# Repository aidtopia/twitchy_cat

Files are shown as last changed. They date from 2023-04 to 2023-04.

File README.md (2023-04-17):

# Twitchy Cat
Adrian McCarthy (mechanics)  
Suzanne Coberly (corpsing)  
based on Oak Lane Cemetery's [Undead Kitty][1]

## The Effect

A rotting corpse of a cat sporadically kicks its hind legs.  It's gruesome and may bother cat lovers.

## Documentation

* [Assembly][2]
* [Corpsing][3]

## Parts

The assembly and corpsing instructions contain lists of all the parts and supplies used for our version.

There are two additional parts that can be printed with a 3D printer.  They are optional, but highly recommended if you're trying to replicate our version.

* Twitchy Cat Link ([STL][4] [SCAD][5]) simplifies fabrication of a reliable linkage
* Handheld Button ([STL][6] [SCAD][7]) provides a tidy case for a push button controller

Oak Lane Cemetery used a prop controller circuit from Jekyll-Labs.  As of this writing, Jekyll-Labs offers a newer version of that circuit called the [Twitchboard][8].

[1]: https://youtu.be/KJrArt0GAYc
[2]: https://github.com/aidtopia/twitchy_cat/blob/main/documentation/twitchy_cat_assembly.md
[3]: https://github.com/aidtopia/twitchy_cat/blob/main/documentation/twitchy_cat_corpsing.docx
[4]: https://www.printables.com/model/455279-twitchy-cat-link
[5]: https://github.com/aidtopia/twitchy_cat/blob/main/parts/twitchy_cat_link.scad
[6]: https://www.printables.com/model/430824-handheld-button
[7]: https://github.com/aidtopia/twitchy_cat/blob/main/parts/handheld_button.scad
[8]: https://www.jekyll-labs.com/p/twitchboard-prop-controller-with.html

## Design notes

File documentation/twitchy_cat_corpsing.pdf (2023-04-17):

## Twitchy Kitty Corpsing & Making Movable Joints

I. First step – Adding movement with actuator and spring (see Adrian’s write up/video)- this could be done later in the process as well, either after making movable joints and dry brushing or after initial corpsing. Either works!

II. Second step – making movable joints and adjusting leg/head position.

a. The way the cat skeleton comes, you cannot move most of the
| joints at all and cannot easily achieve the look of a curled up dead cat as done by Oak Lane Cemetery. The cat has straight legs, and this looks quite different from the classic “undead kitty” (figure 1). If you are OK with this, feel free to skip this step as it does add time; just remember it will be difficult to change your mind after you have done all the corpsing and finishing.

Fig. 1- Top: Unaltered cat skeleton; Middle: “Undead Kitty” from Oak Lane Cemetery after finishing; Bottom: My version of cat skeleton dry brushed with movable joints (back spine has not yet been cut).

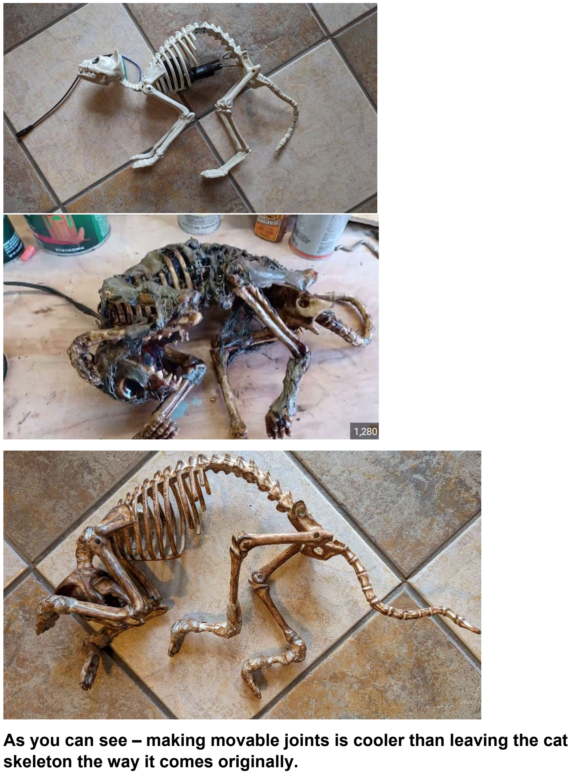
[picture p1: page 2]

As you can see – making movable joints is cooler than leaving the cat skeleton the way it comes originally.

b. Initial steps: Some of the joints (hips, shoulders, front “elbows” and back knees have screws in them and can be unscrewed, but this still doesn’t allow repositioning. Jeff or Adrian can help you carve off some plastic to allow some additional movement and then screw the joints back into the skeleton to reposition the cat limbs, so it is closer to the Oak Lane “dead cat” (fig 2 below). However, in order to get your cat completely poised to look like the undead kitty prop, you will also need to make the solid joints flexible.
c. Making solid joints flexible: For the solid joints on the legs (all four feet and the back “ankles”) and the neck, you will need to cut through the plastic of the joint. The easiest way we’ve found to do this is with a Dremel saw attachment, although a hacksaw will work.

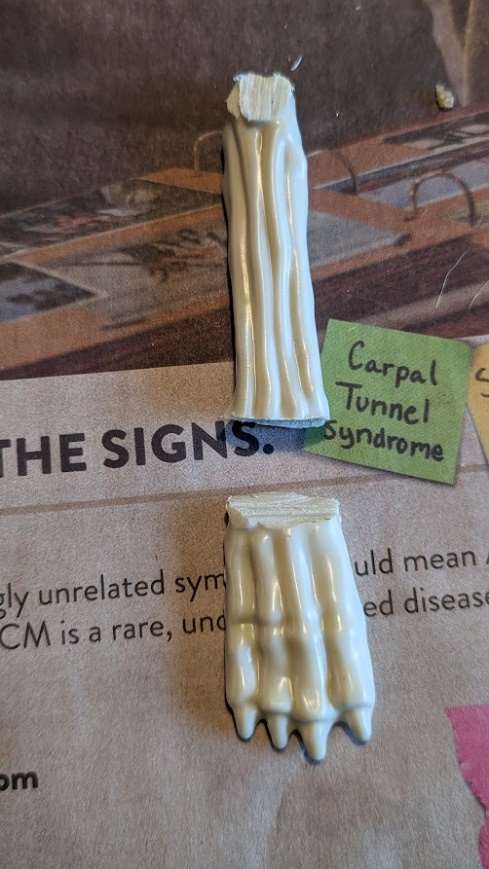
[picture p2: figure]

Once the joints are cut, use flexible wire (0.1 cm flexible armature wire or thin flexible steel wire for floral arrangements works) to wrap around each side of the joint, with one or two strands crossing the joint. Leave some space between the two sides to make sure you can bend the joint to the position you want in the end – test this by bending the joint to the desired position. (See below)

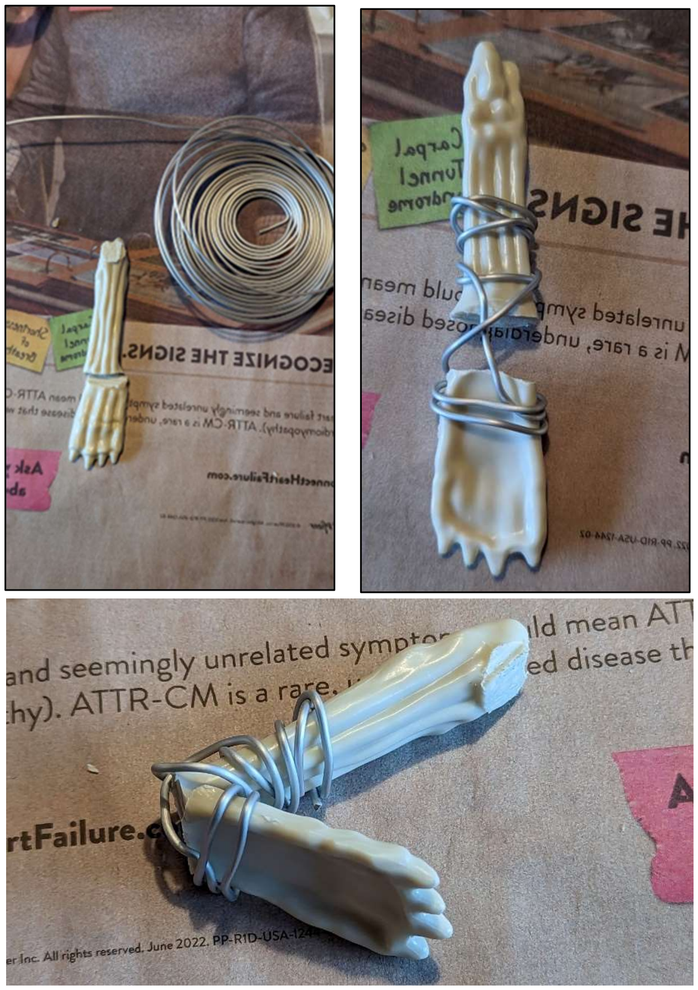
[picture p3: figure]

After this, using the strapping tape, tape over the wire to hold in place. As you do this, continue to bend the joint to the desired position to make sure it will bend this far and loosen the tape as needed. The tape will keep the wire from slipping and will disguise it.
The other leg joints can be done similarly to the above.
d. Head and neck joint: The cat comes with a nonflexible neck that arches up, and a head that can rotate horizontally. In order to make it bend down and match the undead kitty prop, you need to cut the neck near the shoulders (leaving enough spine

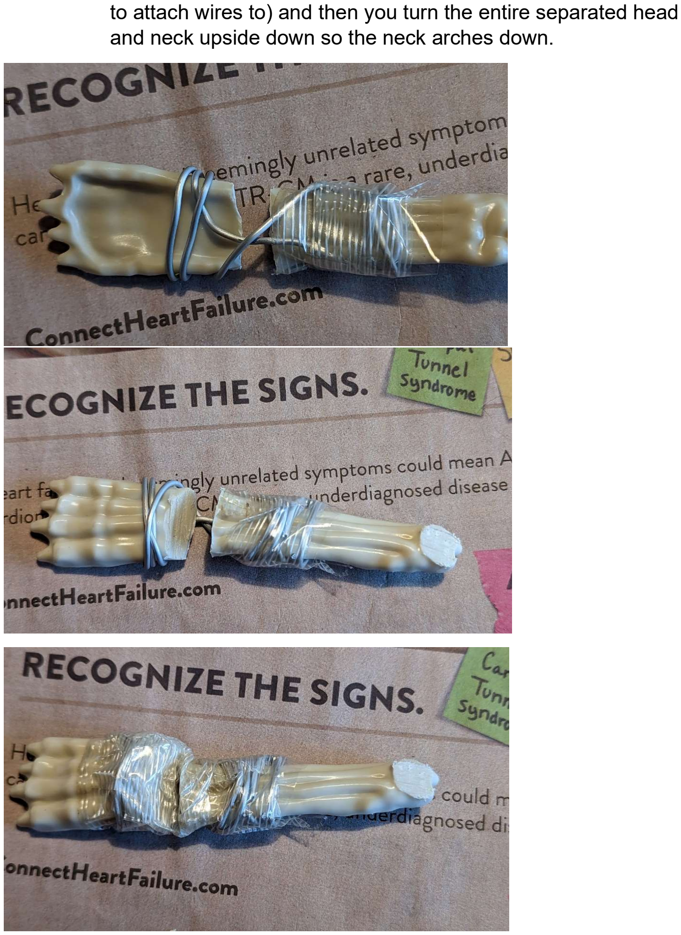
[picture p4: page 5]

to attach wires to) and then you turn the entire separated head and neck upside down so the neck arches down.

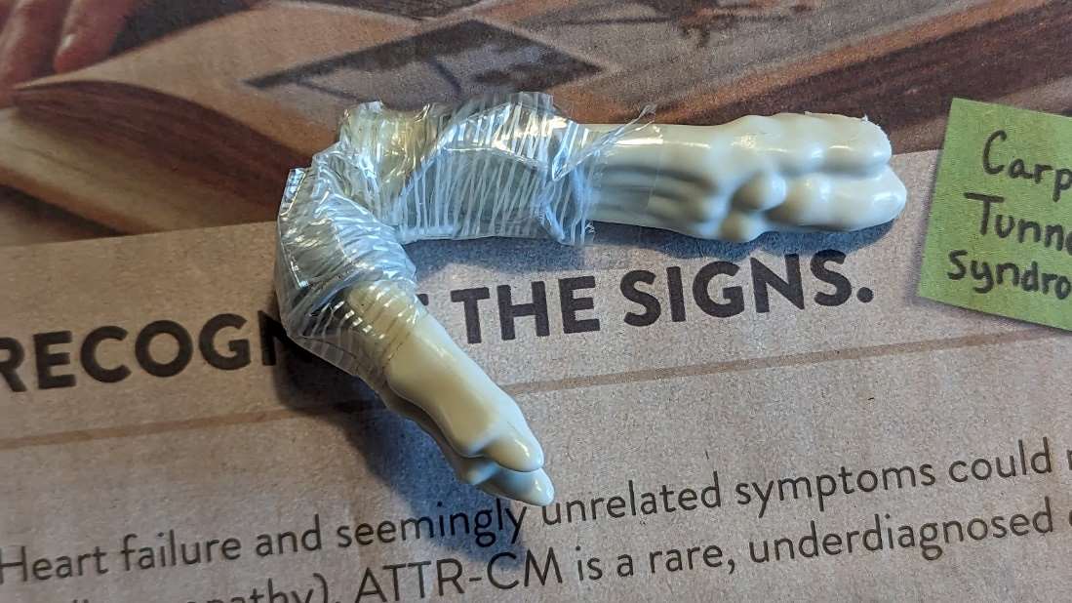
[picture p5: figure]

III. Third step – aging skeleton with dry brushing and creating muscles: Both of these are optional, but if you are letting the bones show through your corpsing (as with the original twitchy kitty), it looks better to age the skeleton first. Cheap white plastic doesn’t look that good. The muscles are definitely optional, but can fill out your cat if you want a more “fresh” zombie cat and it also looks cool to show muscles through the outer corpsed skin. (See the bottom picture)

a. Dry brushing is something many people already know how to
| do, but if you are unfamiliar, here’s the basics.
i. Start with a medium brown and use a very small amount
| of paint on your brush. Either squeeze this out with a paper towel until it is almost dry or sweep it back and forth on newspaper until it is almost dry. Go over your skeleton with a very light touch, not using too much paint, but hitting all areas. This should pick up details and “age” the skeleton. ii. Let this dry; then do the same thing with a lighter cream or very light brown (you can mix cream with a touch of brown or just choose another color that is a very light brown/beige/cream). This “highlights” the skeleton. iii. I usually also then use a darker color brown after this dries to pick up more detail. iv. Go back and forth with each color to get the effect you desire.

v. When you have a good looking “old” skeleton, let dry completely (this doesn’t take long). An example of a dry brushed cat skeleton is the top picture below this section.
b. If you want to make muscles (to see how they look, see the middle picture below this section), it is really easy. Just fold plastic into a rectangular pad of plastic and tape into place (see the picture below or notes in the plastic corpsing instructions to see where to tape them). Then shrink onto the bones a little bit with the heat gun. If you are going to let them show through holes in the “skin”, I would paint them with a dark red (red mixed with brown to the color of old steak) before corpsing.
c. The final picture shows the cat corpsed before painting with some muscles showing through the plastic “skin”.

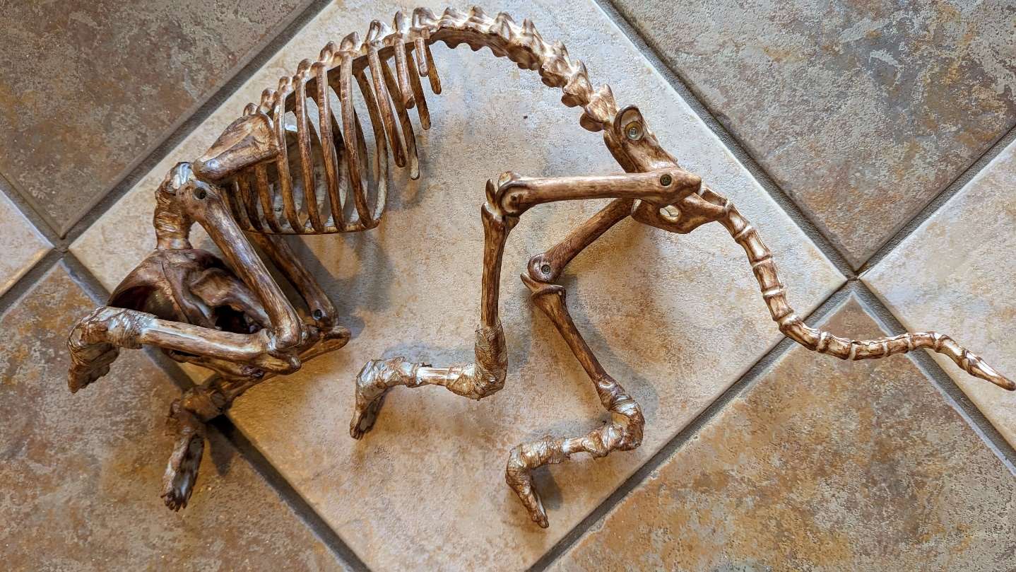
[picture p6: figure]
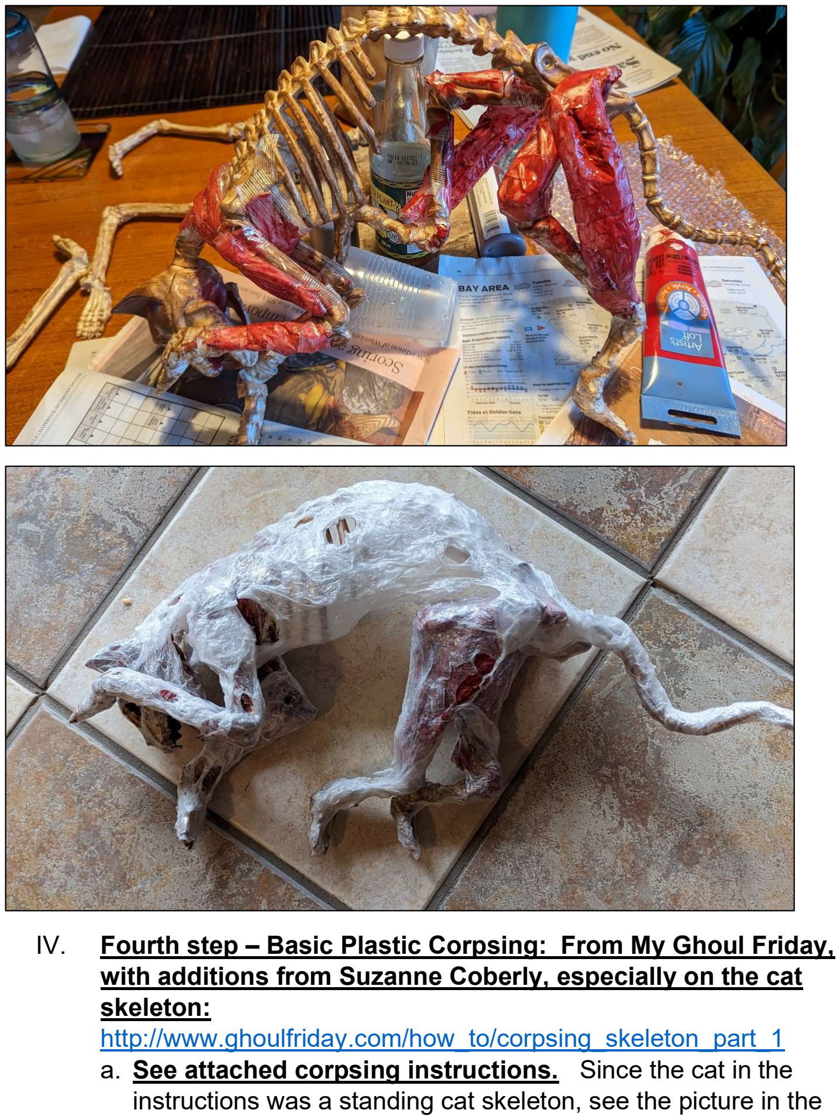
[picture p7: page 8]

IV. Fourth step – Basic Plastic Corpsing: From My Ghoul Friday, with additions from Suzanne Coberly, especially on the cat skeleton: http://www.ghoulfriday.com/how_to/corpsing_skeleton_part_1

a. See attached corpsing instructions. Since the cat in the
| instructions was a standing cat skeleton, see the picture in the

previous section to see what twitchy cat looks like before painting (above).
b. Notes about corpsing for twitchy cat: Since twitchy cat is going to move, you need to be aware that your corpsing will restrict movement. Go ahead and corpse your cat after putting the actuator in, but before painting, you will need to test the movement. If the plastic restricts the movement too much, you can cut (or melt) some plastic away from the restricted area.
c. Finishing the cat: After that, you just paint and dry brush the cat (follow instructions in the basic corpsing) and if too much of the actuator is showing, you can use creepy cloth with latex to hide the actuator (this cloth is flexible and moves with the cat). Hair or eyes can also be added at this time.

Latex covered cloth will take more time to dry, up to a few days if very humid; more typically 1-2 days.

Here’s the corpsed cat with paint, eyes, and drybrushing:

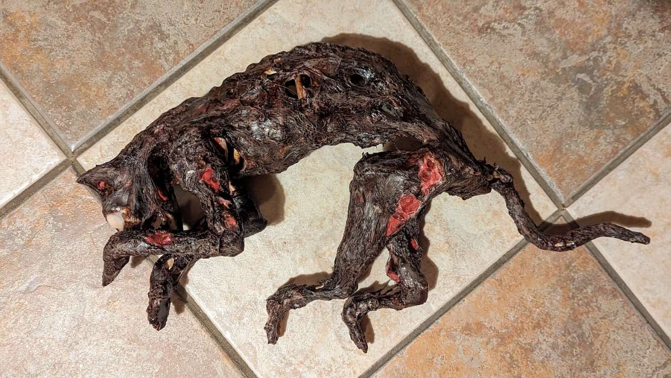
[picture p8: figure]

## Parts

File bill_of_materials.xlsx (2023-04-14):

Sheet: Twitchy Cat
Twitchy Cat Parts and Estimate Cost
Kits Needed | 12
 |  | Item | Source | Units/Order | Price | Shipping | Sales Tax | Cost/Order | Cost/Unit | Units/Kit | Cost/Kit | Needed | On Hand | Short | Orders | Order Cost | Leftovers
Mechanics
 |  | Cat Skeleton | https://www.amazon.com/dp/B00OXD4S5S | 1 | $17.67 | $0.00 | $1.90 | $19.57 | $19.57 | 1 | $19.57 | 12 | 1 | 11 | 11 | $215.26 | 0
 |  | Lock Actuator | https://www.amazon.com/dp/B00P2KANI2 | 4 | $16.99 | $0.00 | $1.83 | $18.82 | $4.70 | 1 | $4.70 | 12 | 4 | 8 | 2 | $37.63 | 0
 |  | Hinge | https://www.homedepot.com/p/Everbilt-1-in-Zinc-Plated-Non-Removable-Pin-Narrow-Utility-Hinges-2-Pack-29277/314150752 | 2 | $2.72 | $0.00 | $0.29 | $3.01 | $1.51 | 1 | $1.51 | 12 | 6 | 6 | 3 | $9.04 | 0
 |  | Spring | https://www.amazon.com/dp/B07NRKNWT6 | 5 | $9.49 | $0.00 | $1.02 | $10.51 | $2.10 | 1 | $2.10 | 12 | 3 | 9 | 2 | $21.02 | 1
 |  | Zip ties | https://www.amazon.com/dp/B08BKSHJ93 | 100 | $4.99 | $0.00 | $0.54 | $5.53 | $0.06 | 4 | $0.22 | 48 | 100 | 0 | 0 | $0.00 | 52
Power
 |  | Power Supply | https://www.amazon.com/dp/B00Z9X4GLW | 1 | $15.99 | $0.00 | $1.72 | $17.71 | $17.71 | 1 | $17.71 | 12 | 0 | 12 | 12 | $212.51 | 0
 |  | Push Button | https://www.amazon.com/dp/B08QV4CWYW | 2 | $8.99 | $0.00 | $0.97 | $9.96 | $4.98 | 1 | $4.98 | 12 | 0 | 12 | 6 | $59.74 | 0
 |  | Barrel Pigtails | https://www.amazon.com/dp/B072BXB2Y8 | 10 | $9.80 | $0.00 | $1.05 | $10.85 | $1.09 | 2 | $2.17 | 24 | 10 | 14 | 2 | $21.71 | 6
 |  | Fuse Holder | https://www.amazon.com/dp/B07MQZ9Q8L | 10 | $10.09 | $0.00 | $1.08 | $11.17 | $1.12 | 1 | $1.12 | 12 | 7 | 5 | 1 | $11.17 | 5
 |  | Fuse 5A | https://www.amazon.com/dp/B083QHC22Q | 10 | $4.99 | $0.00 | $0.54 | $5.53 | $0.55 | 1 | $0.55 | 12 | 6 | 6 | 1 | $5.53 | 4
 |  | 1N4001 Diode |  | 1 | $0.00 | $0.00 | $0.00 | $0.00 | $0.00 | 1 | $0.00 | 12 | 100 | 0 | 0 | $0.00 | 88
 |  | Heat Seal Splices | https://www.amazon.com/dp/B08F479K2R | 100 | $9.99 | $0.00 | $1.07 | $11.06 | $0.11 | 6 | $0.66 | 72 | 90 | 0 | 0 | $0.00 | 18
Corpsing
Norcal Web |  |  |  |  |  |  |  |  |  |  | $2.00
Total |  |  |  |  |  |  |  |  |  |  | $57.29 |  |  |  |  | $593.61

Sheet: SCARY Controller
SCARY Controller
Kits Needed | 10
 |  | Item | Source | Units/Order | Price | Shipping | Sales Tax | Cost/Order | Cost/Unit | Units/Kit | Cost/Kit | Needed | On Hand | Short | Orders | Order Cost | Leftovers
Control Option 1
 |  | Timer Relay | https://www.amazon.com/gp/product/B09XV8KT5H | 2 | $9.99 | $0.00 | $1.07 | $11.06 | $5.53 | 1 | $5.53 | 12 | 1 | 11 | 6 | $66.38 | 1
 |  | JST XH 3-pin | https://www.amazon.com/gp/product/B0B3MW71Q8 | 30 | $8.59 | $0.00 | $0.92 | $9.51 | $0.32 | 1 | $0.32 | 12 | 28 | 0 | 0 | $0.00 | 16
 |  | Barrel Pigtails | https://www.amazon.com/dp/B072BXB2Y8 | 10 | $9.80 | $0.00 | $1.05 | $10.85 | $1.09 | 2 | $2.17 | 24 | 10 | 14 | 2 | $21.71 | 6
 |  | Heat Seal Splices | https://www.amazon.com/dp/B09BJ7FY8X | 100 | $9.99 | $0.00 | $1.07 | $11.06 | $0.11 | 8 | $0.89 | 96 | 90 | 6 | 1 | $11.06 | 94
 |  | Rocker Switch | https://www.amazon.com/dp/B07S2QJKTX | 10 | $7.99 | $0.00 | $0.86 | $8.85 | $0.88 | 1 | $0.88 | 12 | 0 | 12 | 2 | $17.70 | 8
 |  | Fuse Holder | https://www.amazon.com/dp/B07MQZ9Q8L | 10 | $9.39 | $0.00 | $1.01 | $10.40 | $1.04 | 1 | $1.04 | 12 | 8 | 4 | 1 | $10.40 | 6
 |  | Fuse 5A | https://www.amazon.com/dp/B083QHC22Q | 10 | $4.99 | $0.00 | $0.54 | $5.53 | $0.55 | 1 | $0.55 | 12 | 8 | 4 | 1 | $5.53 | 6
 |  | Push Button | https://www.amazon.com/dp/B08R9P9DFC | 6 | $9.99 | $0.00 | $1.07 | $11.06 | $1.84 | 1 | $1.84 | 12 | 4 | 8 | 2 | $22.13 | 4
 |  |  |  |  |  |  |  |  |  |  | $13.23 |  |  |  |  | $154.91

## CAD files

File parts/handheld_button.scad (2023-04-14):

// Handheld Button
// Adrian McCarthy 2023-03-12
//
// Useful for game-show signaling buttons, Halloween prop triggers,
// nurse call buttons, etc.

// High-Amp Button
// https://www.amazon.com/gp/product/B08QV4CWYW
// https://www.chinadaier.com/19mm-push-button-switch/

// Diameter of the body of the button just below the panel. (mm)
Button_Body_Diameter = 19;  // [5:0.5:30]

// Diameter of the flange of the selected button. (mm)
Button_Flange_Diameter = 21.8; // [10:0.1:35]

// Height of the support that holds the button. Should be less than the threaded portion of the button body. (mm)
Button_Support_Height = 5; // [3:1:10]

// Distance from thread to thread on body of the button. (mm)
Button_Thread_Pitch = 1; // [0.5:0.25:3]

// If there's a gap in the threads just below the flange, put its height here. (mm)
Button_Threadless_Height = 1; // [0:0.1:5]

// Diameter of the opening at the small end of the case. (mm)
Cable_Diameter = 6; // [3:0.2:10]

// Thickness of the case. (mm)
Thickness = 2; // [1.2:0.2:4]

// Diameter of the nozzle used for printing. If unknown, the 0.4 mm default is probably fine. (mm)
Nozzle_Diameter = 0.4; // [0.15:0.05:1]

// This creates a tap for cutting an internal thread.  (A nut has
// an internal thread.  A bolt has an external thread.)
// https://en.wikipedia.org/wiki/ISO_metric_screw_thread
module tap(h, d, pitch, nozzle_d=0.4) {
    // An M3 screw has a major diameter of 3 mm.  We're going to
    // nudge it up with the nozzle diameter to compensate for
    // the problem of printing accurate holes and to generally
    // provide some clearance.
    d_major = d + nozzle_d;
    thread_h = pitch / (2*tan(30));
    d_minor = d_major - 2 * (5/8) * thread_h;
    d_max = d_major + thread_h/8;
    
    echo(str("M", d, "x", pitch, ": thread_h=", thread_h, "; d_major=", d_major, "; d_minor=", d_minor));

    x_major = 0;
    x_deep  = x_major + thread_h/8;
    x_minor = x_major - 5/8*thread_h;
    x_clear = x_minor - thread_h/4;
    y_major = pitch/16;
    y_minor = 3/8 * pitch;
    
    wedge_points = [
        [x_deep, 0],
        [x_minor, y_minor],
        [x_minor, pitch/2],
        [x_clear, pitch/2],
        [x_clear, -pitch/2],
        [x_minor, -pitch/2],
        [x_minor, -y_minor]
    ];

    r = d_major / 2;

    facets =
        ($fn > 0) ? max(3, $fn)
                  : max(5, ceil(min(360/$fa, 2*PI*r / $fs)));
    dtheta = 360 / facets;

    module wedge() {
        // TODO:  Figure out how to compute `magic_rotation` angle
        // from the thread pitch and wedge size.  This tilts the
        // wedges so they align well with each other.  The hardcoded
        // value was determined empirically and is probably only
        // appropriate for the threading parameters I've been testing
        // with.
        magic_rotation = 1.35;
        rotate([magic_rotation, 0, 0])
            rotate([0, 0, -(dtheta+0.1)/2])
                rotate_extrude(angle=dtheta+0.1, convexity=10)
                    translate([r, 0])
                        polygon(wedge_points);
    }

    intersection() {
        union() {
            for (theta = [-180 : dtheta : h*360/pitch + 180]) {
                rotate([0, 0, theta]) translate([0, 0, pitch*theta/360])
                    wedge();
            }
            
            cylinder(h=h, d=d_minor);
        }
        cylinder(h=h, d=d_max + nozzle_d);
    }
}

// I've had good results with this in PLA or PETG.  The top that
// has the threads for the button should be sliced with 0.2 mm
// layers (or better).  The case can be sliced with 0.3 mm layers
// for faster printing.
//
// The button body screws into the top piece (flange to flange).
// The rubber ring that comes with the button can be squeezed
// between the flanges for a bit of a seal.  You probably should
// not need the jam nut that comes with the button.  In fact it's
// likely too wide to fit inside the case.
//
// Feed the wires up through the small end of the case and make
// the appropriate connections.  There's enough room inside the
// case to add a diode or resistor.  Use a small (e.g., 4-inch)
// cable tie around the incoming wires as a strain relief.  The
// tie will be too large to be tugged through the narrow end.
//
// The top fits into the case with a friction fit.  You could
// attach it permanently with a couple drops of CA glue.
module handheld_button(
    panel_th=2,
    button_body_d=19,
    button_flange_d=21.8,
    button_support_h=5,
    button_thread_pitch=1,
    button_threadless_h=1,
    small_id=6,
    nozzle_d=0.4
) {
    case_id = button_flange_d - panel_th;
    case_od = case_id + 2*panel_th;
    inset_d = button_flange_d;
    inset_h = button_support_h - panel_th;
    straight_h = 25;
    taper_h = 50;
    total_h = straight_h + taper_h;
    small_od = small_id + 2*panel_th;
    brim_d = min(case_od, 2*small_od);
    
    module case() {
        stop_h = 3*panel_th;
        stop_d = small_id + stop_h/taper_h * (case_id - small_id);

        rotate_extrude()
            polygon([
                [small_id/2, 0],
                [small_od/2, 0],
                [case_od/2, taper_h],
                [case_od/2, taper_h+straight_h],
                [inset_d/2, taper_h+straight_h],
                [inset_d/2, taper_h+straight_h-inset_h],
                [case_id/2, taper_h+straight_h-inset_h],
                [case_id/2, taper_h],
                [stop_d/2, stop_h],
                [small_id/2, stop_h],
                [small_id/2, 0]
            ]);

        // The object above has a tiny footprint, so it doesn't always
        // stick reliably to the build plate.  We can't print it upside
        // down because the inset would become an overhang.  I don't
        // want to mess with slicer settings, so I'm adding a brim here
        // in the design.
        linear_extrude(nozzle_d/2) {
            difference() {
                circle(d=brim_d);
                circle(d=small_id);
            }
        }
    }
    
    module top() {
        body_d = button_body_d;
        support_d = button_flange_d;
        support_h = button_support_h;
        threadless_h = button_threadless_h;

        translate([0, 0, panel_th/2]) rotate([180, 0, 0]) {
            difference() {
                union() {
                    // lip
                    difference() {
                        cylinder(h=panel_th, d=case_od, center=true);
                        translate([0, 0, -panel_th])
                            cylinder(h=panel_th, d=case_id);
                    }
                    // support for the body of the button
                    translate([0, 0, panel_th/2-support_h])
                        cylinder(h=support_h, d=support_d);
                }
                translate([0, 0, panel_th/2-support_h-0.1]) {
                    // cut threads into the support
                    tap(h=support_h+0.2, d=body_d,
                        pitch=button_thread_pitch, nozzle_d=nozzle_d);
                    if (threadless_h > 0) {
                        translate([0, 0, support_h-threadless_h])
                            cylinder(h=threadless_h+panel_th/2+0.1, d=body_d);
                    }
                }
            }
        }
    }
    
    offset = (case_od + brim_d)/2 + 1; 
    translate([0, offset, 0]) case();
    top();
}

handheld_button(
    panel_th=Thickness,
    button_body_d=Button_Body_Diameter,
    button_flange_d=Button_Flange_Diameter,
    button_support_h=Button_Support_Height,
    button_thread_pitch=Button_Thread_Pitch,
    button_threadless_h=Button_Threadless_Height,
    small_id=Cable_Diameter,
    nozzle_d=Nozzle_Diameter,
    $fn=$preview ? 30 : 60
);


// Parameters for other buttons:

// Metal Button
// https://www.chinadaier.com/gq12h-10m-momentary-push-button-switch/
//   Spec says M12 without specifying pitch.  Using microscope and test
////   prints, I determined it's 0.75.
// Button_Body_Diameter = 12;
// Button_Flange_Diameter = 13.9;
// Button_Support_Height = 5;
// Button_Thread_Pitch = 0.75;
// Button_Threadless_Height = 1;

// Arcade Button
// https://www.adafruit.com/product/3489
//
// Button_Body_Diameter = 28;
// Button_Flange_Diameter = 33.3;
// Button_Support_Height = 10;
// Button_Thread_Pitch = 2;
// Button_Threadless_Height = 3;

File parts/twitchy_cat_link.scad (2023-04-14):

// Twitchy Cat Link
// Adrian McCarthy 2024-04-13
//
// Manually fabricating the necessary link for the Twitchy Cat Halloween
// prop was too error prone.  This design constrains some of the unwanted
// degrees of freedom and makes the mechanism work reliably.  It also
// gives a nearly ideal place to anchor the spring for the return action.

module twitchy_cat_link(l=25, th=3, nozzle_d=0.4) {
    no6_free_d = 0.1495 * 25.4 + nozzle_d;
    no6_head_d = 0.270 * 25.4 + nozzle_d;
    no6_head_h = 0.097 * 25.4 - nozzle_d;
    no6_nut_d = (5/16 * 25.4 + nozzle_d) / cos(30);
    no6_nut_h = 7/64 * 25.4 - nozzle_d;
    nose_w = 5;
    nose_d = 12;
    zip_w = 5 + 3*nozzle_d;
    zip_th = 2 + 3*nozzle_d;
    notch_w = nose_w + nozzle_d;
    notch_d = nose_d + 2;
    w    = max(th + notch_w + th, no6_head_h + 1.2 + notch_w + 1.2 + no6_nut_h);
    base = min(no6_nut_d + 4*nozzle_d, notch_d);
    translate([0, 0, base/2]) rotate([90, 0, 0]) {
        difference() {
            linear_extrude(w, convexity=8, center=true) {
                difference() {
                    hull() {
                        translate([l, 0]) circle(d=base, $fs=nozzle_d/2);
                        square([0.1, base], center=true);
                    }
                    translate([l, 0]) circle(d=no6_free_d, $fs=nozzle_d/2);
                }
            }
            translate([l, 0, 0]) {
                translate([0, 0, w/2-no6_head_h])
                    cylinder(h=no6_head_h+0.1, d=no6_head_d, $fs=nozzle_d/2);
                cylinder(h=notch_w, d=notch_d, center=true, $fs=nozzle_d/2);
                translate([0, 0, -(w/2+0.1)]) rotate([0, 0, 30])
                    cylinder(h=no6_nut_h+0.1, d=no6_nut_d, $fn=6);
            }
            translate([-(25-th)/2, 0, 0]) rotate([90, 0, 0])
                cylinder(h=base+0.1, d=25, center=true);
            translate([-(25-th)/2, 0, 0]) rotate([90, 0, 0]) {
                linear_extrude(zip_w, convexity=8, center=true) {
                    difference() {
                        // High $fn because the cable tie needs a smooth
                        // channel.
                        circle(d=25+th+zip_th, $fn=180);
                        circle(d=25+th, $fn=180);
                    }
                }
            }
        }
    }
    spring_d = 10;
    spring_offset = 30-22/2;
    wing_w = base;
    linear_extrude(th, convexity=8) {
        translate([l/2, 0, 0])
            polygon([
                [0, spring_offset],
                [-wing_w/2, base/2-0.1],
                [ wing_w/2, base/2-0.1],
                [ th, spring_offset+0.5*th],
                [-th, spring_offset+1.5*th],
                [-1.5*th, spring_offset+th]
            ]);
    }
}

twitchy_cat_link();

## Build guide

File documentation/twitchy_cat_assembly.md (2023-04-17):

# Twitchy Cat Assembly
Adrian McCarthy (mechanics)  
based on Oak Lane Cemetery's [Undead Kitty][1]

This covers the assembly of the Twitchy Cat mechanism.  Suzanne Coberly has an excellent set of instructions for [posing and corpsing][12] the cat.

See https://www.github.com/aidtopia/twitchy_cat for the latest version of this document.

The first draft was distributed at the Northern California Haunters Group's March 2023 Make &amp; Take.  This substantially more complete draft is from April 2023.

## The Effect

A rotting corpse of a cat sporadically kicks its hind legs.  It's gruesome and may bother cat lovers.

## Parts

* [cat skeleton][2]
* [car door lock actuator][3] (with hardware)
* [1" hinge with screws][4]
* [spring][5]
* 8" cable ties
* [12V/8A DC power supply][6]
* [DC barrel connectors][7]
* inline fuse holder with 5A fuse (recommended)

But that's not all!

I recommend soldering wires and insulating them with heat-shrink tubing.  If soldering is not your thing, you can use [heat-shrink butt-splice connectors][8] that include a ring of low temperature solder in the middle.

You will also need a controller of some kind.  I'll cover how to put together a push button for manual control, using a [3D-printed case][9].  For the push button, you'll need:

* [3D-printed button case][9]
* [push button][11]
* 1N4001 or similar rectifier diode (recommended)

I'll also show how you can wire your cat to various prop controllers.

To make your skeleton look good and creepy, you'll need additional supplies covered in the [corpsing instructions][12].

### Linkage Options

The original version of these instructions explained how to fabricate a link from the brass rod that comes with the door lock actuator.  That can work.  However, the resulting linkage can be finicky.  In the worst case, it might buckle, locking up the mechanism in such a way that manual intervention is required.  I no longer recommend this method.

Instead, I recommend using this [3D-printed link][10] instead.  The printed link constrains the mechanism, ensuring that the actuator movement is translated into the kicking motion, without twisting and slipping that can happen with the old method.  The printed link also provide a better place to attach the spring.

The link can be printed with PLA filament, but I recommend PETG for more durability.  I got good results with 0.2 mm layer height.

To use the PRINTED LINK you will need:

* [3D-printed link][10]
* #6-32 x 1/2" machine screw
* #6-32 hex nut
* an extra cable tie

Norcal Haunters: You can get the PRINTED LINK parts from me, along with instructions on how to swap it in for the ROD LINK.

To use the ROD LINK you will need the brass rod the comes with the door lock actuators.

### Skeleton Selection

The salient features of the cat skeleton are that it be about 14", have an arched back, and that the rib cage ends by the middle of the spine.  I've seen a few that have unrealistically long rib cages that reach almost to the back legs.  Those won't work.

The Amazon link provided is a bit of a pot luck.  That supplier seems to have two similar-but-different models and ships whichever one is on hand:

* The GREEN skeletons are cast in a matte off-white plastic and dry-brushed with a greenish tint.  They have no wire in the tail.  The pelvis is upside down (the spine passes under the pelvic bone).  The greenish tint looks like it might be glow-in-the-dark paint, but&mdash;alas&mdash;it's not.

* The WHITE skeletons are cast in a glossy white plastic.  They have a wire in the rubbery tail to make it poseable, and the pelvis orientation is anatomically correct.

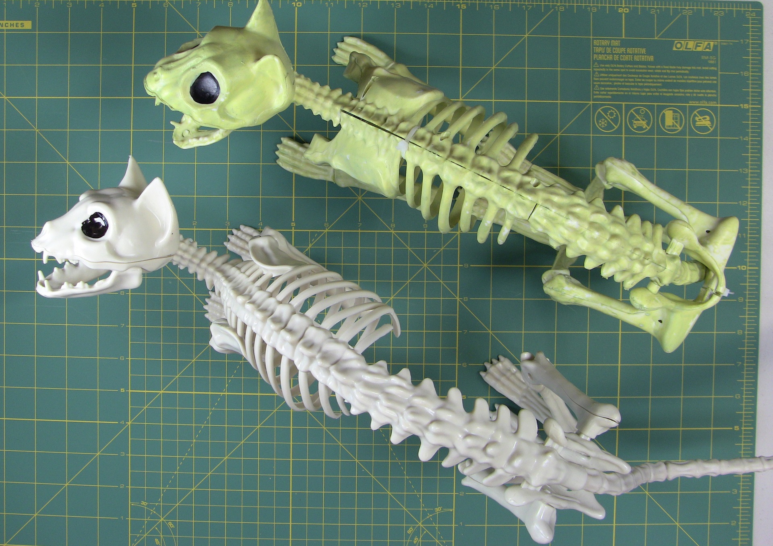
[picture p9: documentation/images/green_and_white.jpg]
Two models of cat skeleton The green and white cat skeletons


**Either will work for this project.**

## Tools

* phillips screwdrivers, #0, #1, and #2
* something pointy to make a small divot in the plastic
* a drill
* 1/16" drill bit
* a small hacksaw or similar
* wire cutters
* wire strippers
* heat gun
* soldering iron and solder (optional if you use the heat shrink splices)
* painters tape (optional)

For the ROD LINK you will also need:

* 1/8" drill bit
* felt tip marker (e.g., a Sharpie)
* a vise (to hold the rod while you bend it)
* a hammer
* small bolt cutters or a hack saw

## Steps

NOTE:  These steps assume the DISPLAY SIDE is the cat's left side.  If you corpse the cat all around, it doesn't much matter which side is the display side.  You might, however, want to do thorough corpsing on the display side and less on the other side so you can keep access to the mechanism.

### Posing the Tail

WHITE skeletons have wire inside the tail, so you can pose it later.  You may, however, want to remove the hind legs before moving on to **Adding the Hinge**.

GREEN skeletons do not have a wire in the tail, but there is a slight curl to it.  If it's curling down and you'll want it to curl up, (or vice versa), you can flip it around.  This requires disassembling the pelvis.

* Loosen the two screws that hold the hips together, using a philips #0 screwdriver (manual, not electric).
* Snip the cable tie (if there is one).
* Pull off the right side of the hip and its leg.
* Swivel the left side to revealing another small screw into the side of the spine just above  the tail.  Loosen that and remove the hip.
* Now you can remove the tail, flip it 180 degrees, and reinstall it.

**Pro tip:**  Consider postponing reassembly of the hips until after you've got the actuator installed.  Just don't lose the screws!

### Adding the Hinge

Oak Lane Cemetery hinged the spine by cutting it in two, drilling holes through each end, and reconnecting them with a cable tie (or two cable ties?).  That's easy to do, but I found that left too much play side-to-side, which caused the mechanism to bind.

My solution is to instead use an actual hinge.  Installing it requires a bit of dexterity, but I've learned that installing the hinge _before_ cutting the spine makes it manageable.

With the cat on its back, lay the open hinge on the spine, just beyond the last rib.

* On the GREEN skeletons, you'll probably find that the hinge will fit right behind the last rib, possibly just touching it.  If it doesn't fit there, it's fine to choose the next vertebra.

* On the WHITE skeletons, you'll almost certainly have to leave a one vertebra gap between the last rib and the hinge.

The pin of the hinge should be on the abdominal side, not against the spine itself.  The pin should be oriented so that it's perpendicular to the spine.  The flaps of the hinge with the screw holes should be on the wider parts of the vertabrae with the pin aligned with the narrow space in between.  

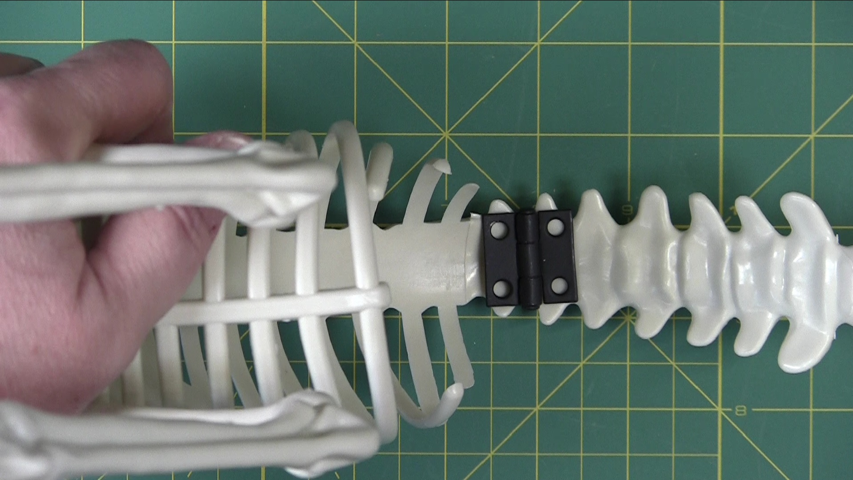
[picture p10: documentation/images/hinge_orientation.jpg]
Hinge position and orientation


**Pro tip:**  Use some tape to temporarily hold the hinge in place.

Mark the spine through the centers of the screw holes with something sharp, like a punch or an awl.  That'll help keep the drill bit from skidding as you begin to drill.

Drill 1/16" pilot holes for the screws.  If the holes start right at the edge of the spine, you can angle them in toward the center a bit, so that the screws will have more plastic to dig into.

**CAUTION:**  Be aware of what's on the other side of the spine as you drill.  If you drill all the way through the spine (which is not necessary), you could drill into your hand or your table if you're not careful.

Use a hand screw driver to start one of the hinge screws into one of the holes.  Once you have the first one started, start the next one diagonally across.  Once you have all four started, double check the position of the hinge and then tighten them all down.

Careful! Especially on the WHITE skeletons, you may find that the tips of some of these screws go all the way through spine.  You can file the tips down.  Later you may want to cover it with some kind of filler (like sculpting epoxy).  Either way, the corpsing should hide it.

Remove the tape.

### Cutting the Spine

Turn the cat upright and cut through the spine in line with the hinge pin.

I recommend almost any small hand saw.  A few people had luck with a rotary tool (like a Dremel) on the WHITE skeletons, but I found the plastic was deeper than the cutting discs could reach on the GREEN ones.

Once you cut through, the hinge should allow you to bend the back of the spine toward the front of the cat.  If there's any binding, you might try shaving a little plastic away at the cut line.

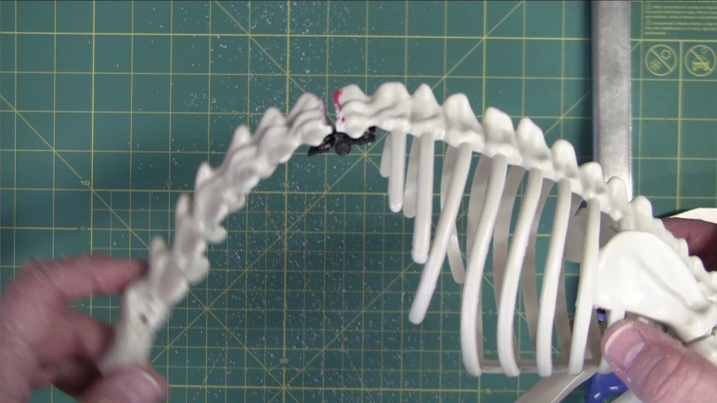
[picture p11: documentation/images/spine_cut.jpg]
The spine has been cut at the hinge spine severed at the hinge


### Preparing the Actuator

It's easier to perform these steps on the actuator before installing it into the rib cage.

#### Adding the Power Connector

Snip the connectors off the actuator's wires.

When power is applied, we want the actuator to extend, not retract.  With the actuators I use, the proper connections are:

* positive (RED) to BLUE wire on the actuator
* negative (BLACK) to the GREEN wire on the actuator

If your actuator's wires are a different color, you'll have to briefly activate the actuator with a power supply to figure out which polarity causes the actuator to extend.

Select a DC barrel receptacle.  Make sure you use the kind that your power supply would plug into, not the one that matches your power supply.  (People often use the words _male_ and _female_ to distinguish between mating connectors.  With these kinds of connectors, however, those terms can be counter-intuitive.)

Connect the wires to the receptacle using your favorite technique.

The actuator uses a remarkably high current, so it's important to have a good electrical connection.

* Proper soldering makes the best electrical connection, and you can then insulate that connection with heat shrink tubing.

* If soldering is not in your skill set, you can use the heat shrink butt-splice connectors that have the low temperature solder ring on the inside.

* I do not recomment wire nuts or crimp connectors for this connection.  If you want a temporary connection, lever nuts (e.g., Wago 221 Compact) are good, but you'll have to do that after installing the actuator since the lever nuts will not fit through the collar bone.

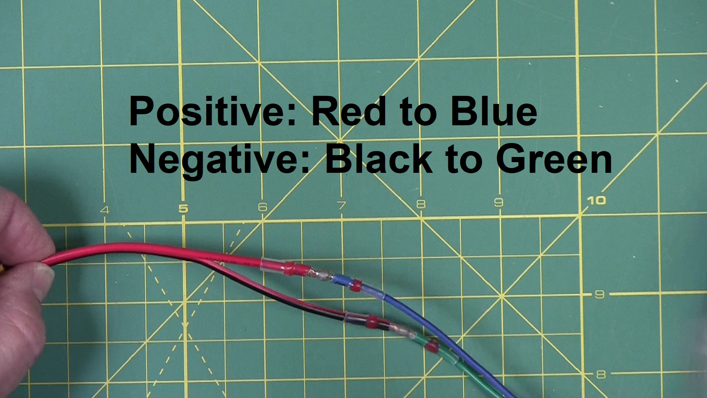
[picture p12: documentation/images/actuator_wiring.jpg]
Actuator Wiring Wiring a barrel connector to the actuator


Note that DC barrel receptacles are not waterproof.  If you intend to operate your twitchy cat in a damp environment, substitute waterproof connectors or skip the connectors altogether and splice long wires all the way back to the controller.  In that case, make sure you use waterproof heat shrink to insulate the wire connections.

#### Pre-installing the Screw

Hold the actuator in your hand as though it's a sci-fi ray gun.  The long axis is the barrel of the gun, and the short one is the handle.  The moving end of the actuator should be pointing away from you.  Mark the forward mounting hole on your right side.  That's the one we're going to use to anchor the return spring.

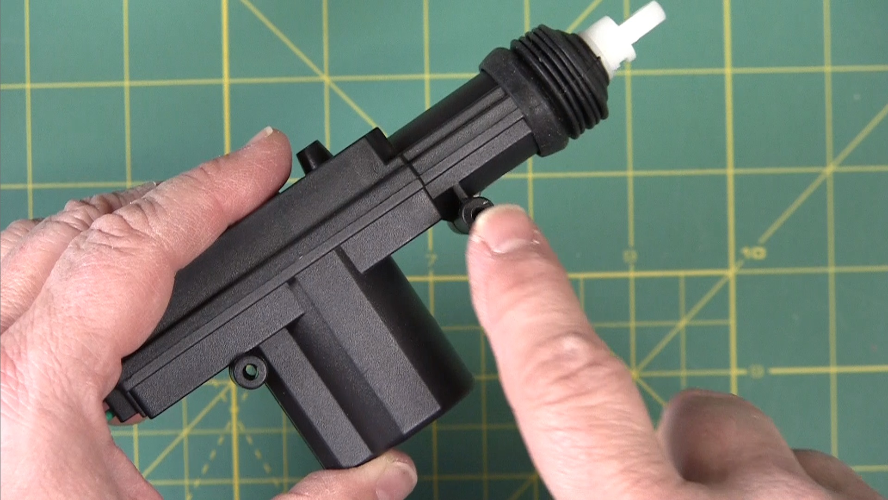
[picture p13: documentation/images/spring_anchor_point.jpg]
Locating the screw to anchor the return spring on the actuator


Screw one of the larger screws that came with your actuator into the marked mounting hole.  The hole is not threaded, but the screws are self tapping.  Start slowly with a hand screw driver.  Leave the head of the screw protruding about 1/8".  Later, this will be the mounting point for one end of the spring.

#### Connecting the Printed Link

For the ROD LINK, skip this step.

For the PRINTED LINK, slip a cable tie through the channel near the end of the link.  Push most of the tie through, so that the "head" of the tie is close to the side of the link with the wing.  Do not zip the tie closed.  That'll come later.

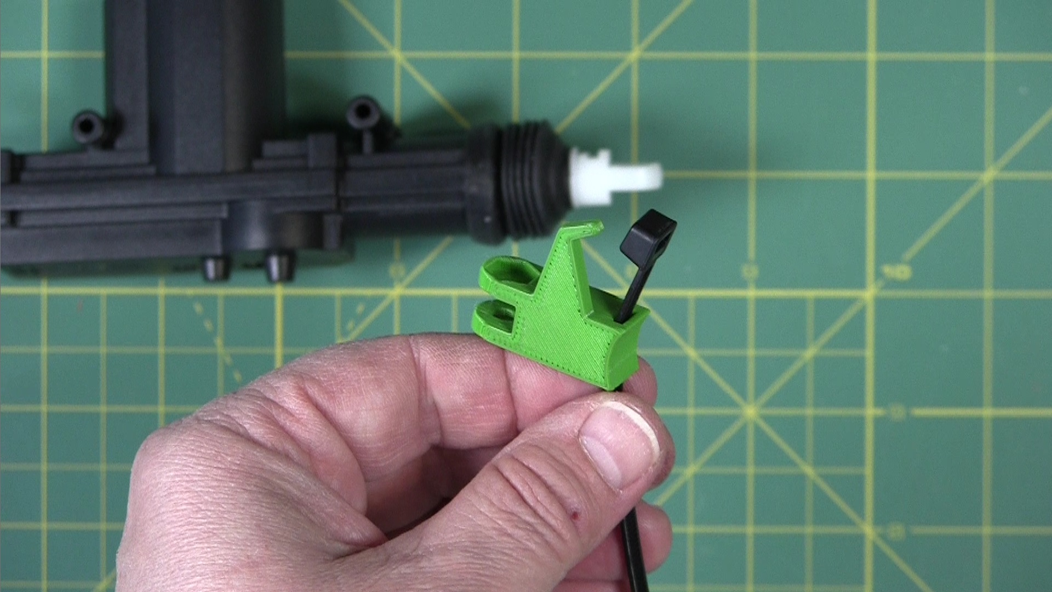
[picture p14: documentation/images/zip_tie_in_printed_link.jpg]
Note the orientation of the cable tie in the 3D printed link Load an 8 inch cable tie in the channel until the head is near the wing


As you hold the #6 hex nut in the hexagonal recess in the link, slip the link over the "nose" of the actuator and secure with the half-inch screw.  Do not over-tighten.  The link should swing freely at the end of the actuator.

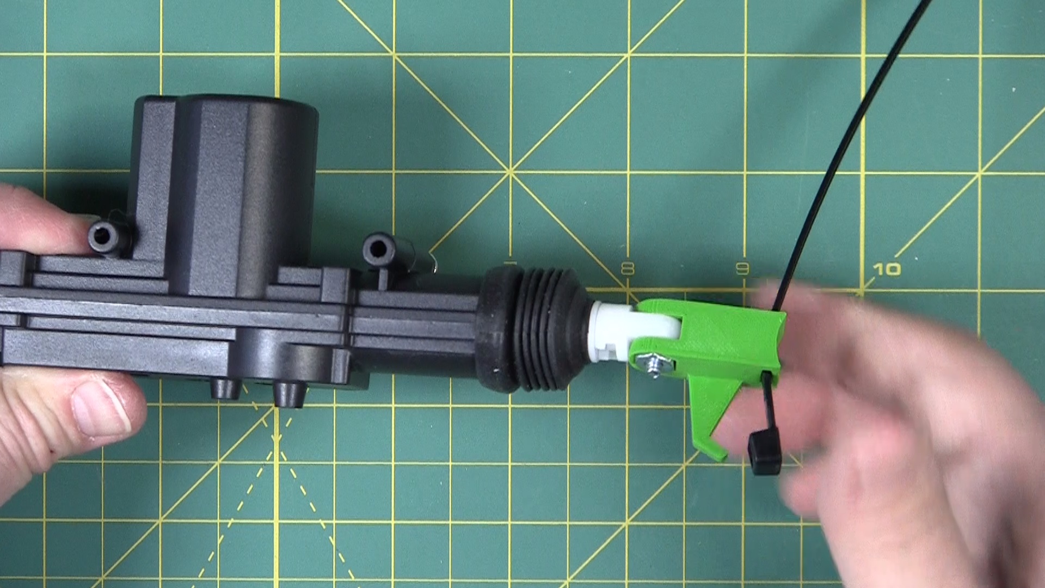
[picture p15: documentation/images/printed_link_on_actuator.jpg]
The printed link attached to the actuator The printed link is attached to the nose of the actuator with a #6 machine screw and hex nut.


### Installing the Actuator

The door lock actuator is installed in the rib cage.  I tried several different orientations, but the one used by Oak Lane Cemetery worked the best.

We're going to hold it in place with two cable ties.  In most cases, an 8" cable tie is sufficient, but some found they needed an 11" one.  The cable ties are going to encirle the long axis of the actuator to hold it against the sternum.  And they are going to be positioned one either side of the short cylinder part to keep the actuator from sliding forward and backward.

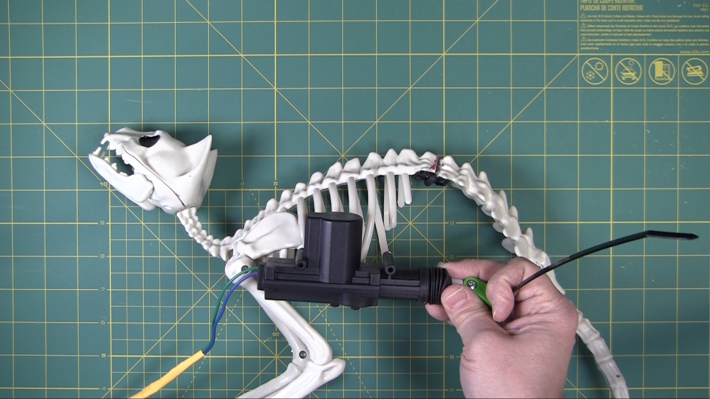
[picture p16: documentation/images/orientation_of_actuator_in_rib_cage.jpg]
Orientating the actuator Orienting the actuator


This step also requires a little dexterity.  As with the hinge step, you may find it much easier to leave the back legs off for now.  Also remember the cable ties are cheap and if you mess up, you can just snip them off and try again.

First insert a cable tie through last rib space below the shoulder until it exits the rib cage on the other side.  Push most of the slack in, the zip tie will flex upward until it touches the spine, leaving a clear path for the actuator.

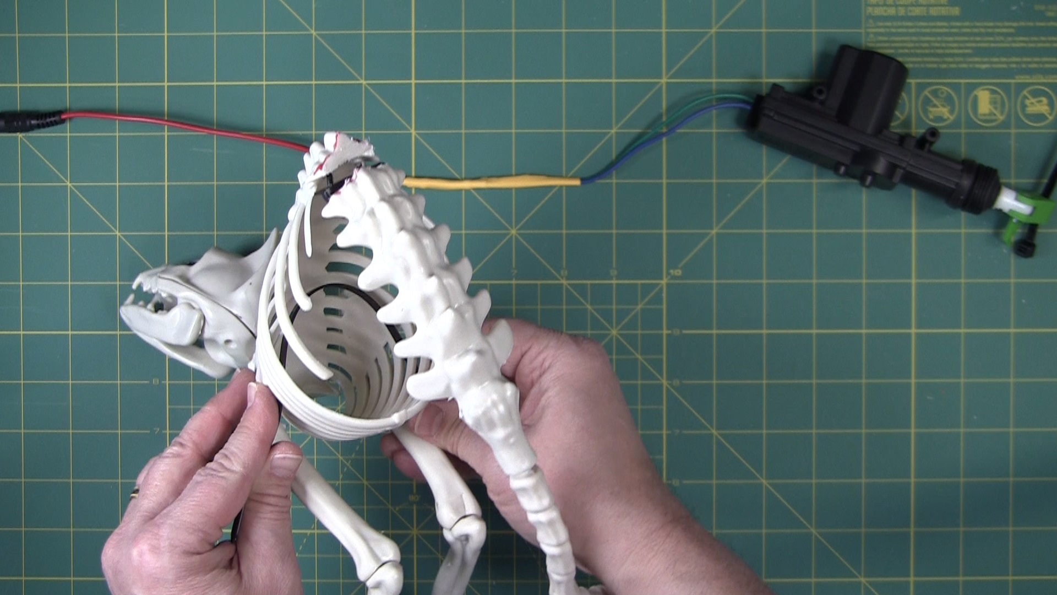
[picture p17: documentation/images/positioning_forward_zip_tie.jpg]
Pushing the slack for the front zip tie makes room to insert the actuator The front zip tie is the tricky one


Insert the actuator into the rib cage, wires first.  Guide the wires through the collar bone.  When it's in as deep as it can go, zip the cable tie so that it holds the actuator against the inside of the sternum.

Feed the second zip tie between the ribs and cinch it down.

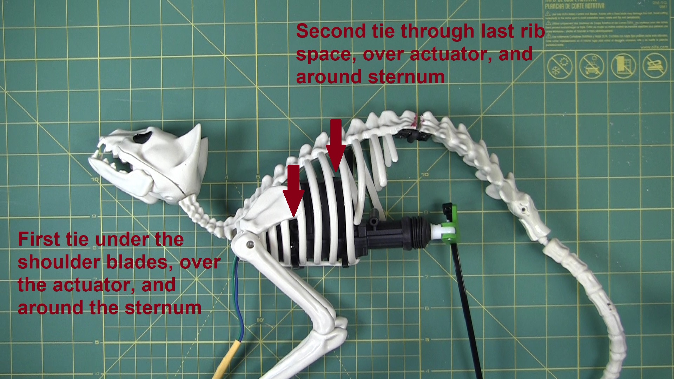
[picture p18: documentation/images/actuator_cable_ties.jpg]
Securing the actuator with two cable ties


The actuator should now be in line with the sternum.  If it twists or wiggles side-to-side, tighten up the cable ties.  If it slides forward and backward, check that you have a tie right in front of and another right behind the cylindrical part of the actuator (the handle of your ray gun).  If it's not firmly in place, snip the ties and try again.

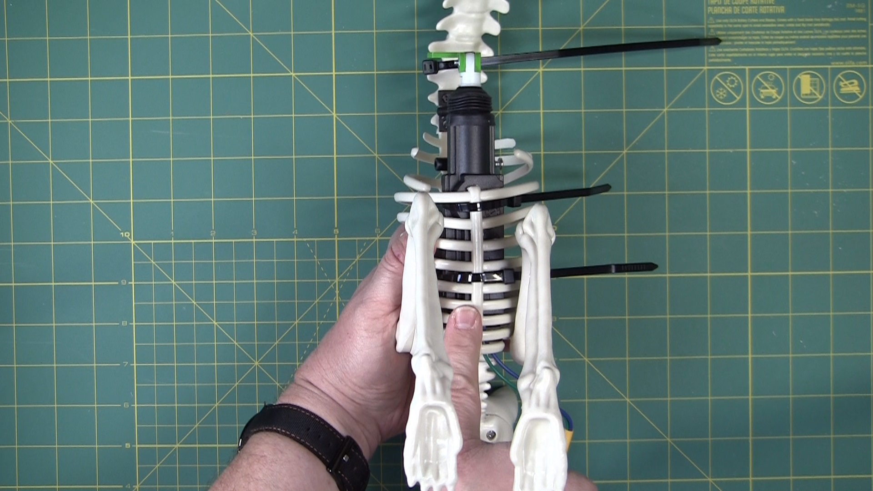
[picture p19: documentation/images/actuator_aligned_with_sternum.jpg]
Ensure the actuator is aligned with the sternum


Also ensure that the wires have come through the collar bone.

### Attaching the Printed Link to the Spine

For the ROD LINK, skip this step.

Note that the nose of the actuator swivels.  Turn it now so that the head of the #6 screw faces the display side of the cat and the wing of the printed link faces the opposite direction.

With the actuator fully retracted, pull the hind legs forward.  Rotate the printed link counterclockwise until you find the first spot on the spine where the free end is perpendicular to the spine.  This should be just above the hip bone.  Wrap the cable tie around the spine and secure it tightly around the narrow space between two vertebrae.

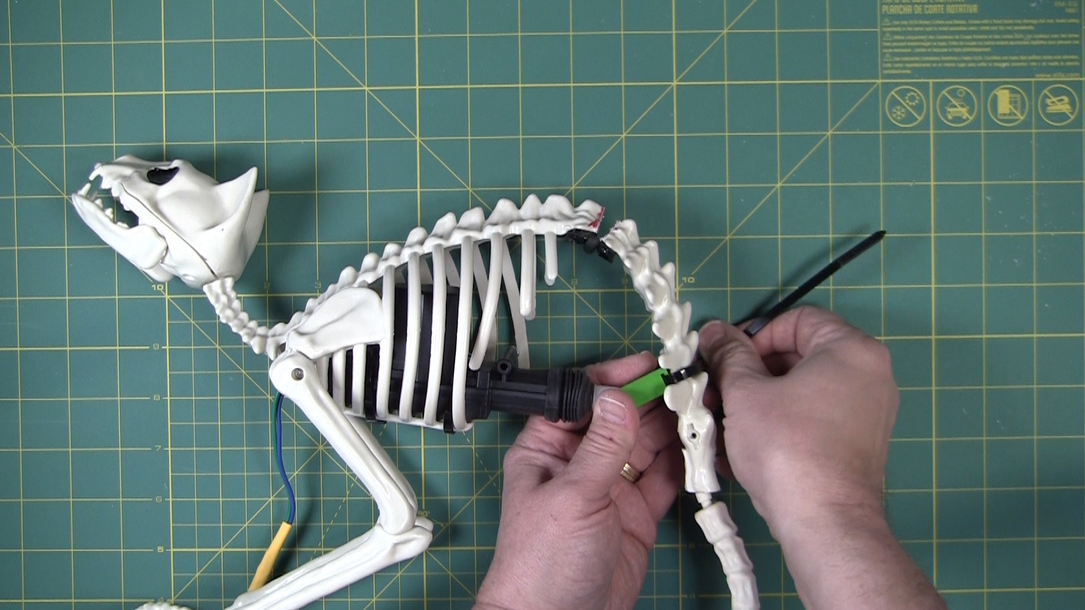
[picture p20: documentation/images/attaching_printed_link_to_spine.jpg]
Attaching the printed link to the spine


Manually move the actuator though its entire range of motion and make sure there is no binding.

### Reattaching the Rear Legs

If you removed the rear legs earlier, now is the time to reattach them.  Just reverse the steps given at the beginning.  If you lost a screw or you break something, don't fret.  Cable ties, hot glue, or sculpting epoxy can usually put Humpty Dumpty back together again.  Kludges can be hidden during corpsing.

### Making the Rod Linkage

If you're using the PRINTED LINK, skip this step.

If you're using the ROD LINK, get ready to bend some metal.

_TODO:  Add photos throughout this section._

The actuator hardware pack includes a brass rod with a bend and a cap at one end.  If yours is lost or damaged, you can make your own from coathanger wire.  (Better yet, get your hands on a PRINTED LINK instead!)

Starting from the left side of the cat, feed the straight end of rod through the nose of the actuator until you twist it at the bend.  The cap will keep that end in the actuator.

Pull the hind legs as far forward as you can.

Keeping the actuator retracted, move the rod until it lines up with the wide part of one of the vertabra on the right side of the cat.  You should choose a vertabra that keeps the rod almost inline with the actuator but slightly above it.

Use a felt marker to mark the rod where it touches the tip of the vertebra.

Clamp the rod in a vise at your mark.  Make a crisp 90° bend so that the back end is parallel to the end with the cap.

You want the end you just bent to extend about 1/2 to 3/4 inch.  Using small bolt cutters or a hack saw, trim off the excess.  You might want to file down any sharp points left by the cut.

Put your modified rod into the actuator and again line it up with the selected vertebra.  Looking at the bottom of the cat, estimate how much you will need to cut off of the wide part of the vertebra so that the rod can be parallel to the actuator.  Trim the tip off of the selected vertebra using a small saw, a utility knife, or a file.

Drill a 1/8" hole in the center of the trimmed tip.  Insert the cut end of the rod into that hole.

Looking from the bottom again, check that the rod is now parallel to the direction of the actuator.  Make adjustments as necessary.  You might need to shave more off the tip of the vertebra, drill the hole deeper, or trim the back end of the rod a bit more.

Holding the front end of the cat, you should be able to manually extend and retract the actuator and the hind legs should move accordingly.  If it's tight, look for ways to reduce the friction, such as further trimming or widening the hole.

### Wiring the Push Button

Even if you plan to use a programmable controller later, it's handy to have a push button controller for testing.

I'll assume you're using the 3D-printed button case and the recommended parts.

Norcal Haunters:  Your buttons are pre-wired.

We're going to wire the button with DC barrel connectors.  The power supply will connect to one and the other will connect to the actuator.

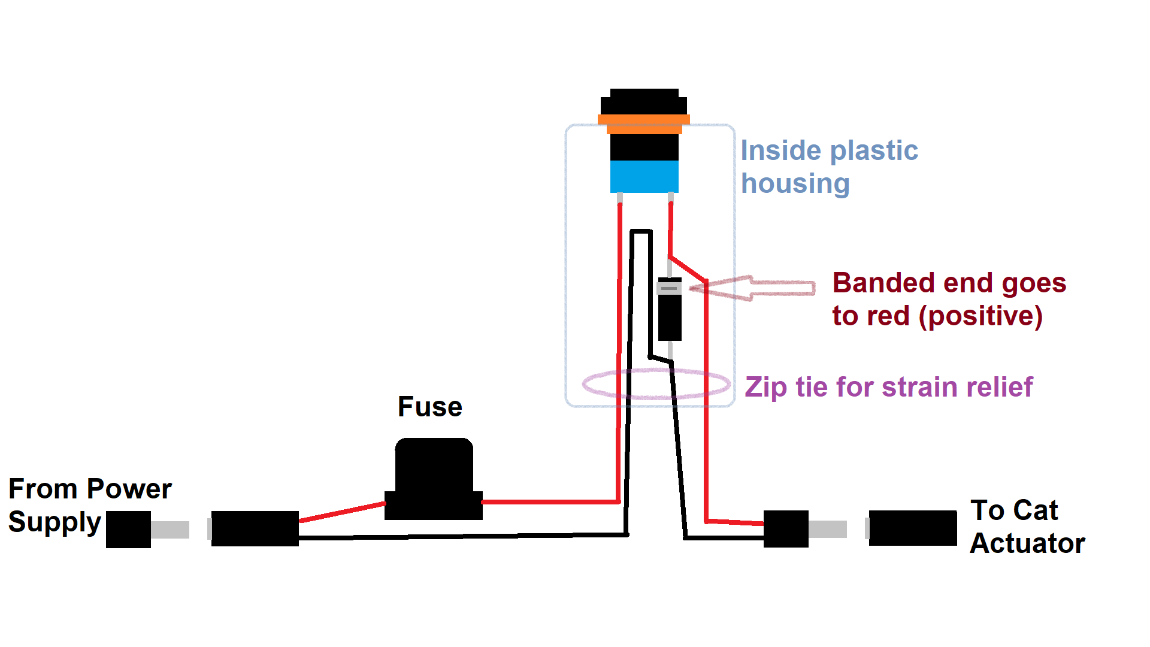
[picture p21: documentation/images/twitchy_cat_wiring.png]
Twitchy Cat wiring diagram Twitch Cat wiring diagram


Push the wires from the DC barrel connectors through the narrow end of the 3D-printed case until they extend out the top by roughly the length of the case.  Use a small zip tie to create a strain relief.

Unscrew the jamb nut from the bottom of the button body.  If the button has a rubber O-ring, leave that cinched up against the flange.  Screw the button all the way into the small 3D-printed ring.

Note that the recommended button is rated for 10 amps.  The actuator draws 5-6 amps, which is more than many small push buttons are designed to handle.  This button has screw terminals, and the wires are stranded, so best practice is to crimp ferrules onto the wire ends before attaching them to the button.  Tinning them with a little solder will do in a pinch.

Now make the connections that happen inside the button case per the wiring diagram.  The black wires connect to each other.  Each red wire connects to a terminal on the bottom of the button.

I highly recommend adding a flyback diode as shown in the diagram.  When the actuator turns off, the diode will safely dissipate the energy stored in the actuator's coils.  Pay close attention to the diagram to make sure you get the diode in the correct direction.

Norcal Haunters:  Your pre-wired buttons have the diodes in place.

Gently pull the wires at the small end of the case while guiding the ring holding the button into the top of the case.  It should make a good friction fit.  If you want to make it more secure (and permanent), a couple drops of super glue (cyanoacrylate) should bond the two plastic parts.  The small zip tie should be sufficient strain relief, but a blob of hot glue at the small end will provide additional relief and help keep dust out.

### Testing the Kick Action

Connect the power supply to the appropriate connector on the button assembly.  Then connect the other connector to the one on the actuator.

CAUTION:  The actuator may be powerful enough to hurt a stray finger.  Keep your fingers away from any pinch points whenever the actuator might be triggered.

Briefly press the button, and the actuator should extend, causing the hind legs to kick.  Sometimes, this action is sharp enough that the mechanism will bounce, causing the actuator to retract most of the way.  Manually put the actuator back into its retracted position and try it again.  You should be getting a nice sharp kick without binding or buckling.

CAUTION:  Do not hold the button down.  When the actuator reaches its limit (which takes less than 1/10 second), it will draw its maximum current.  That causes the motor inside to heat up and it could burn itself out.  Short presses are best.

### Installing the Spring

The actuator could be powered in both directions, but that requires a motor driver (or multiple relays).  To keep things simple, we've wired the actuator to extend when it's activated, and we'll use a spring will pull it back when the power is switched off.

Hook one end of the spring to the screw you installed in the actuator.

For the PRINTED LINK, hook the other end of the spring onto the wing of the printed link.  The spring should be just slightly stretched when the actuator is fully retracted.  If you push the hind legs back and then release them, the spring should provide enough force to reliably retract the actuator.  You're ready to skip to the next step.

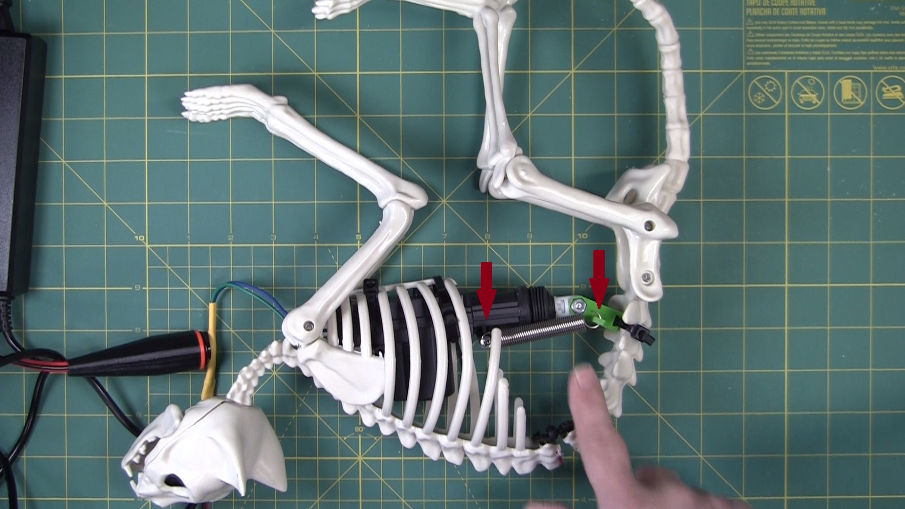
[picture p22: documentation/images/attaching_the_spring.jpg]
Attaching the spring with the printed link


For the ROD LINK, you need to find the best spot on the spine to anchor the spring.  This takes trial and error.

Holding the free end of the spring at the tips of the vertebra, try to find one that provides enough force to reliably retract the actuator but not so much force that extending the actuator is difficult.  The first vertebra above where the link connects is a good first guess.

You can create a spring anchor point by using another one of the screws that came with your actuator.  Trim the NON-DISPLAY SIDE tip of a vertebra to make a flat surface.  Drill a 1/16" pilot hole into the plastic and manually drive in the screw.

Using your push button, test the kick action.

* If the kick seems sluggish or doesn't reach its full extent, the spring is too tight.  Try anchoring the spring on a higher vertebra or add a loop of cable tie to the end of the spring and hook that over the anchor.

* If the kick is sharp but the retraction isn't reliable, the spring is too loose.

* If the actuator is shifting around in the rib cage (or bending it), there's too much tension, or the spring is pulling up or down more than forwards.

Don't worry if you have to make more holes in the skeleton.  These anchors are on the NON-DISPLAY SIDE, and mistakes are easy to hide or fix in the corpsing process.

### Using a Controller

_TODO:  Wiring diagram for PicoBoo-like controllers_  
_TODO:  Information about Jeckyll-Labs Twitchboard_  
_TODO:  Warning against long activations_  

### Posing and Corpsing

If it's all working well, proceed to Suzanne's [posing and corpsing][12] instructions to turn your twitching lump of plastic into an unsettling animatronic.

## Links

If you're reading the paper version of this, here are the links:

* Oak Lane Cemetery's Undead Kitty https://youtu.be/KJrArt0GAYc
* cat skeletons on Amazon https://www.amazon.com/dp/B00OXD4S5S
* car door lock actuators on Amazon https://www.amazon.com/dp/B00P2KANI2
* 1-inch hinges at The Home Depot https://www.homedepot.com/p/Everbilt-1-in-Zinc-Plated-Non-Removable-Pin-Narrow-Utility-Hinges-2-Pack-29277/314150752
* springs on Amazon https://www.amazon.com/dp/B07NRKNWT6
* 12V/8A DC power supply on Amazon https://www.amazon.com/dp/B00VA2K0MK
* DC barrel connectors on Amazon https://www.amazon.com/dp/B072BXB2Y8
* solder seal heat-shrink butt splice connectors on Amazon https://www.amazon.com/dp/B08F479K2R
* handheld button case on printables.com https://www.printables.com/model/430824-handheld-button
* link for Twitchy Cat on printables.com https://www.printables.com/model/455279-twitchy-cat-link
* push buttons on Amazon https://www.amazon.com/dp/B08QV4CWYW
* Posing and Corpsing Instructions: https://github.com/aidtopia/twitchy_cat/blob/main/documentation/twitchy_cat_corpsing.pdf

[1]: https://youtu.be/KJrArt0GAYc
[2]: https://www.amazon.com/dp/B00OXD4S5S
[3]: https://www.amazon.com/dp/B00P2KANI2
[4]: https://www.homedepot.com/p/Everbilt-1-in-Zinc-Plated-Non-Removable-Pin-Narrow-Utility-Hinges-2-Pack-29277/314150752
[5]: https://www.amazon.com/dp/B07NRKNWT6
[6]: https://www.amazon.com/dp/B00VA2K0MK
[7]: https://www.amazon.com/dp/B072BXB2Y8
[8]: https://www.amazon.com/dp/B08F479K2R
[9]: https://www.printables.com/model/430824-handheld-button
[10]: https://www.printables.com/model/455279-twitchy-cat-link
[11]: https://www.amazon.com/dp/B08QV4CWYW
[12]: https://github.com/aidtopia/twitchy_cat/blob/main/documentation/twitchy_cat_corpsing.pdf

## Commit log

2023-02-16 Actually added the parts spreadsheet.
    [parts.xlsx]
2023-02-26 Updated parts spreadsheet to keep and eye on costs.
    Broke the "fancy" controller out to a separate page.
    [parts.xlsx]
2023-04-14 Added 3D printable link for Twitchy Cat mechanism.
    [twitchy_cat_link.scad]
2023-04-14 Fixed a link or two in the parts list.
    [parts.xlsx]
2023-04-14 Renamed parts spreadsheet to bill_of_materials.xlsx.
    [bill_of_materials.xlsx]
2023-04-14 Copied the STL file for the handheld button to parts.
    [handheld_button.scad]
2023-04-15 Added images (and some corrections) to the assembly documentation.
2023-04-15 Correction: Recommended power supply is 8 amps, not 6.
2023-04-15 Did light editing on the assembly instructions.
2023-04-17 Updated links now that the link is posted on printables.com.
